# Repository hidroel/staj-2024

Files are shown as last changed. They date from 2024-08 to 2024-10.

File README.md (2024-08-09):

# Proje Başlığı: Damlama Sulama Sistemi Ek Modülü

## 1. Giriş
### 1.1 Proje Tanımı
Müşterimiz, tarım sulama sisteminde kullandığı damlama sulama sistemi ile ilgili bir sorun yaşamaktadır. Bu proje, bu sorunu tespit etmek ve çözmek amacıyla yürütülecektir.

### 1.2 Amaç ve Hedefler
Projenin amacı, damlama sulama sisteminin çalışmasında aksamaya neden olan problemleri belirlemek ve bu problemleri çözmektir. Hedefler:
- Problemin nedenlerini belirlemek
- Çözüm önerileri sunmak
- Çözümün uygulanabilirliğini test etmek
- Nihai çözümü uygulamak

## 2. Mevcut Durum Analizi
### 2.1 Problemin Tanımı
Müşterimiz, dizel su pompası çalışmakta iken su çekilen kanalda suyun kesilmesi sonucunda santifüj'ün susuz kalarak boşta çalıştığını ve yaklaşık 30 saniye sonra yanarak kullanılamaz hale geldiğini belirtmiştir. Su pompasında barometre olmasına rağmen sistemin otomatik olarak durmasını sağlayan bir araç bulunmamaktadır. Başlatma ve durdurma işlemleri tamamen manuel olarak yapılmaktadır. Müşterimiz su kesintisi durumunda sistemin durmasını ve kendisine SMS bilgilendirmesi gelmesini istemektedir.

### 2.2 Önceki Çalışmalar
Konuyla ilgili daha önce herhangi bir modül tasarımı ve uygulaması yapılmamıştır. Yalnızca geçici çözüm olarak müşterimiz su pompasının başında bekleyerek basınç düştüğünde sistemi durdurmaktadır. Bu çözüm iş gücü gerektirmesi ve efektif olmamasından dolayı müşterimiz için kabul edilmemektedir.

## 3. Çözüm Önerileri
### 3.1 Olası Nedenler ve Çözümler
Sorunun nedenleri:
- Su çekilen kanalda belirsiz saatlerde su kesintileri olması.
- Santrifüj'ün boşta çalıştığında fazla sürtünme yapması ve aşırı ısınmasın.
- Su kesintilerinin önceden bildirimi yapılmayıp tamamen plansız olması.

Çözüm Önerileri:
- Su kesintisi önceden biliniyorsa bu saatler aralığında su pompasının çalıştırılmaması.
- Su basıncının entegre bir sistem ile sürekli kontrol edilerek su kesintisi veya azalması durumunda sistemin otomatik olarak kendini durdurması.

### 3.2 Çözümün Uygulanması
En verimli çözüm belirlenmiştir ve çözümün uygulama adımları aşağıdaki gibidir:
1. Su pompası üzerinde bulunan barometre tamamen analog çalıştığı için ek bir basınç sensörü eklenecektir.
2. Basınç sensörü kanaldan gelen hortum üzerinde olacak ve su boşluğu pompaya varmadan önce durumu sisteme bildirebilecektir.
3. Basınç sensöründen uyarı geldiği anda dizel motor durdurulacak ve su çekme işi son bulacaktır.
4. Dizel motorun durdurulabilmesi için yapılacak bağlantı su pompasının aç-kapa anahtarlamasına bağlanacaktır. Su pompası dijital olarak durdurabilecektir.
5. Sistemin durmasının hemen ardından müşteriye SMS iletilecektir.

## 4. Beklenen Sonuçlar ve Ölçümler
### 4.1 Beklenen Sonuçlar
Çözüm yöntemimiz uygulandığında su kesintileri hangi saat aralığında olursa olsun kesinti olduğu anda su pompası otomatik olarak duracak ve sistemin susuz kalmasından dolayı oluşan tüm problemlerden kaçınılacaktır. Ayrıca müşteriye giden SMS sayesinde müşterimiz sistemin durduğunun haberini alarak sulama programını buna göre ayarlayabilecektir.

### 4.2 Başarı Kriterleri

- Su pompasının hiçbir bileşenlerinin susuz kalma sonuçlarından olumsuz etkilenmemesi.
- Müşterinin sulama durduğuna dair bilgiyi eksiksiz ve zamanında alması.

## 5. Zaman Çizelgesi

1. Problemin Analizi: 1 hafta
2. Çözüm Önerilerinin Geliştirilmesi: 1 hafta
3. Çözümün Uygulanması: 2 hafta
4. Test ve Gözlem: 1 hafta
Toplam: 5 hafta

## 6. Kaynaklar ve Bütçe
Projede kullanılacak malzemeler, hizmet ve işçilik maliyeti gibi değişkenler listelenecek ve toplam hesap çıkartılacak.

Tahmini bütçe: HESAPLANACAK

## 7. Kullanılacak Bileşenler

- 1x ADC
- 1x Röle
- 1x MCU (STM32F103RC)
- 1x GSM Modülü (SIM800L HZ-MG2608-C1A-MK-02)
- Yakıt Kesici (UNOX 24V DC Normalde Açık Solenoid Valf)
- 1x Basınç Sensörü (DFRobot SEN0257)
- 3x LED
- 3x Buton

### MCU İçin Gerekli Pinler
- 1x I2C
- 1x SPI
- 4x UART

### Bileşenlerin Kullanım Sebepleri

Proje diyagramında görüldüğü gibi, sistemin çalışma prensibi istenmeyen durum oluştuğunda motorun durdurularak pompanın kapanmasıdır. Kullandığımız basınç sensörü 0-16 bar aralığında olup düzenli ve sık aralıklarla suyun basıncını ölçecektir. Su kesildiğinde hat içerisinde basınç düşecek ve basıncın düşmesi MCU tarafından algılanacak ve valfe bağlı röle tetiklenecektir. Rölenin tetiklenmesi sonucunda normalde açık olan özelliğe sahip valf kapanacak ve dizel motora yakıt akışı duracaktır. Bu sayede dizel motor stop ederek santifüj'ün yanmasını engelleyecektir. MCU röleyi tetiklerken aynı zamanda GSM modülüyle haberleşme sağlayarak müşterimizin telefonuna bildirim SMS'i gitmesini sağlayacaktır.

## 8. Projenin Genel Çalışma Prensibi

Projenin sözel açıklaması şu şekildedir:

MCu'yu barındıran kart ve diğer tüm ek bileşenler dizel motorun aküsünden beslenecektir. Motora ait olan kontak akü ile modüller arasında bağlantıyı sağlamaktadır. Dizel motorun yakıt tankı ile motor arasında bulunan yakıt hortumuna solenoid valf eklenecektir. Bu valf projenin maliyetini düşürmek amacıyla normalde kapalı olarak belirlenmiştir. Solenoid valfin Vin bağlantısı MCU üzerindeki rölenin NC bacağına bağlıdır. Rölenin Common bacağı ise aküden güç almaktadır. Bu sayede, ek modülün herhangi bir sebeple devre dışı kalması durumunda dahi rölede güç akışı devam edecek ve normalde kapalı özelliğe sahip olan valf açık durumda (Yakıt geçişi mümkün) olacaktır.

Projeye özel olarak tasarlanan ek modül kartı, basınç sensörü ile 0-5v protokolü kullanarak analog haberleşme yapacaktır. 2 saniyelik periyotlar ile basınç sensöründen veriler alınarak ADC ile MCU'ya iletilecektir. MCU tarafından basınç kontrol edilerek, istenilen değerin altına düşmesi durumunda röle tetiklenecek ve dizel motor stop ettirilecektir. Bununla eş zamanlı olarak UART ile GSM modülü haberleşmesi sağlanacak ve belirlenen telefon numarasına durumla ilgili SMS gönderilecektir.

Manuel olarak kontak kapatıldığı durumda aküden gelen güç kesildiği için tüm sistem devre dışı kalacaktır. Ayrıca normalde kapalı olan valf herhangi bir tetikleme almadığı için kapalı konuma geçecektir. Bu sayede dizel motor kapalı durumdayken ekstra güvenlik sağlanmış olacaktır.
## 9. Sonuç ve Öneriler
Bu projede belirtilen çözüm adımları doğru bir şekilde uygulandığında ve gerçek uygulama testi analizlerdeki gibi gittiğinde müşterinin tüm sorunu ortadan kaldırılacaktır. Bununla birlikte, sistem uzaktan başlatma ve durdurma gibi ileriye dönük gelişmelere açıktır. Tamamen manuel olarak çalışan su pompası bu entegre ile birlikte durdurma işlemi kontrol edilebilir hale gelmiştir. İleriye dönük eklemeler ve güncellemelerle sistem insan gücünü daha az harcayacak duruma getirilebilir.

Müşteriye eklenen sensörlere ve kartlara zarar vermemesi, afaki koşullarda bulundurmaması için gerekli uyarılar yapılmalıdır. Projede kullanılan akü, kablo gibi zaman içerisinde yıpranan ve ömrünü tüketen materyaller hakkında düzenli bakım yaptırması belirtilmelidir.

Bu projede 0-5v analog haberleşme protokolü ve çevre bileşenlerle seri haberleşme protokolleri uygulanmıştır. Bunlarla alakalı detaylı bilgiye ulaşmak için:

[Seri Haberleşme Dökümanı](https://github.com/hidroel/staj-2024/blob/main/documents/serial.md)
[Analog Haberleşme Dökümanı](https://github.com/hidroel/staj-2024/blob/main/documents/analog.md)

Projede kullanılacak kartın diyagrami aşağıdadır:

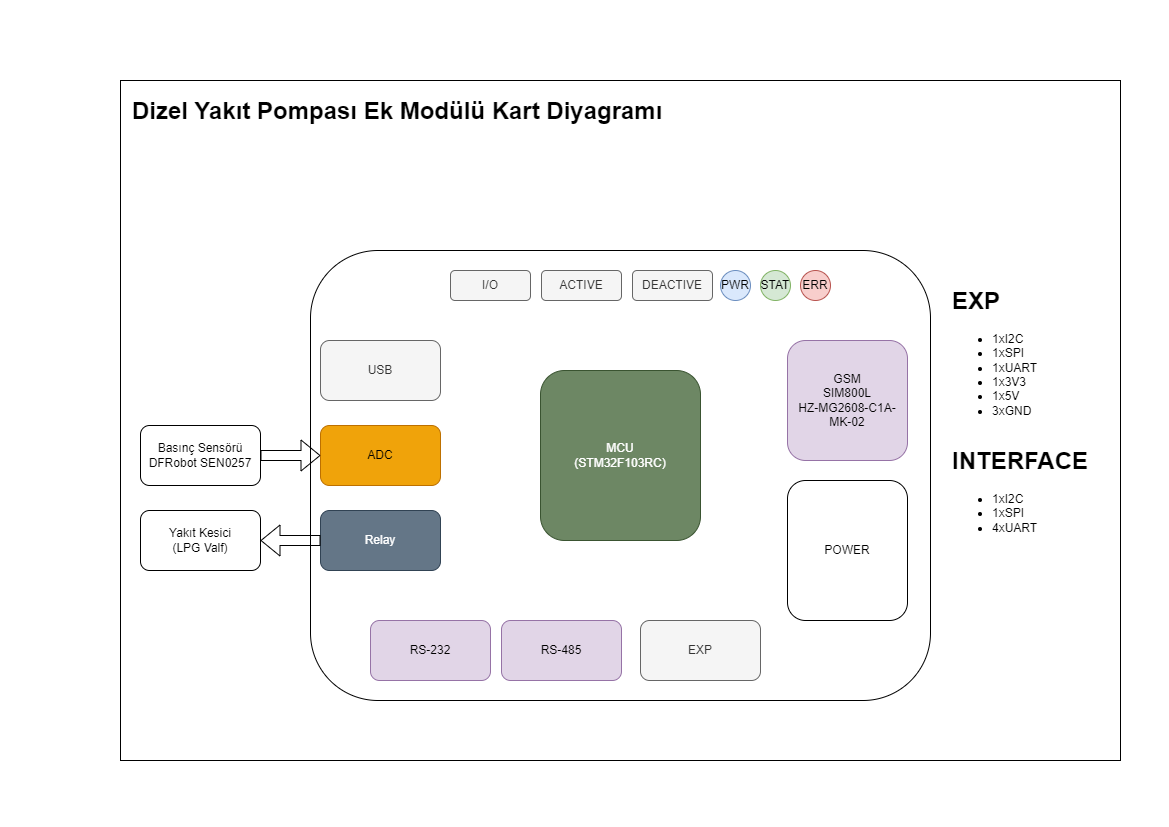
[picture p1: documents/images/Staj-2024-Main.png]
Main Diyagram


Projenin çalışma prensibini açıklayan diyagram aşağıdadır:

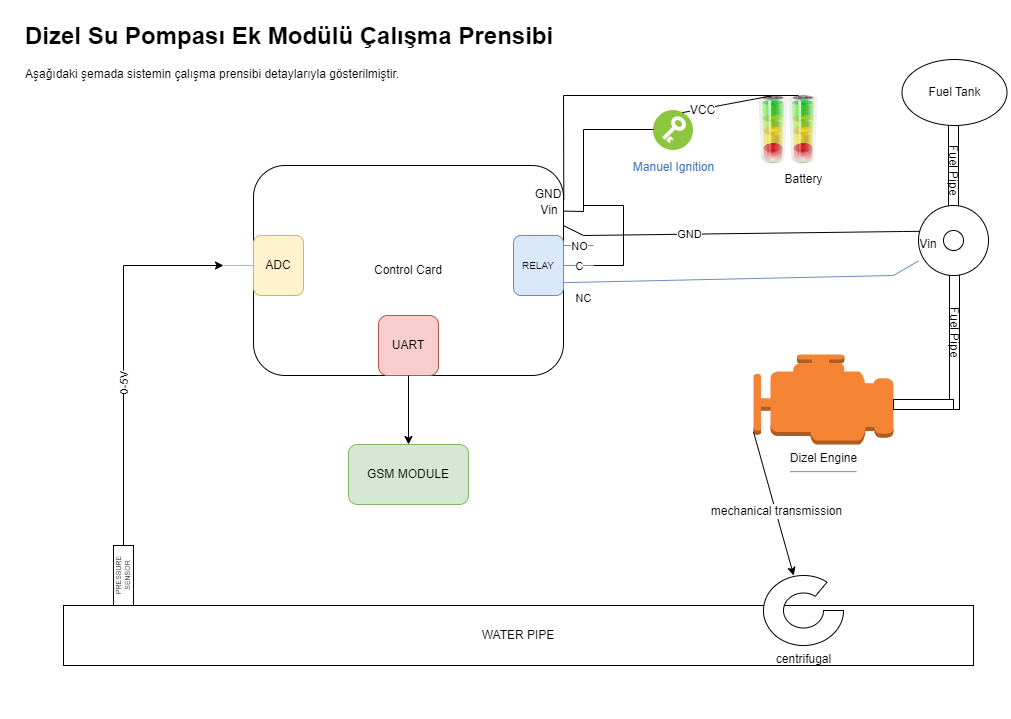
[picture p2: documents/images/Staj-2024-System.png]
System Diyagram


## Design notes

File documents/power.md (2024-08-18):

# Power Devresi Nedir?
Power devresi, bir elektronik sistemin tüm bileşenlerine gerekli enerjiyi sağlamak için tasarlanmış bir devredir. Elektronik cihazların düzgün ve güvenilir bir şekilde çalışabilmesi için doğru voltaj ve akım değerlerinin sağlanması kritik öneme sahiptir. Power devresi, bu ihtiyacı karşılamak için güç kaynaklarını düzenler, dönüştürür ve filtreler. Kart üzerindeki en önemli devredir ve sistemin işleyişi için hayati önem taşır. Power devresinde kullanılan bileşenler şunlardır:

- Güç Kaynağı: Sistemin ana gücünü aldığı ekipmandır. Adaptör, akü, pil, batarya gibi herhangi bir şey olabilir.
- Dönüştürücüler: Sistemdeki bileşenlerin ihtiyacı olan voltaj her zaman güç kaynağı ile aynı değildir. Bu nedenle voltajı istenilen seviyelere çevirmek için dönüştürücüler kullanılır. Ayrıca, AC güç kaynağı varsa DC'ye çevirir.
- Filtreler: Gürültü ve dalgalanmaları azaltarak stabil bir güç sağlar. Kapasitörler ve indüktörler ile oluşturulan filtre devreleri ile bu sağlanır.
- Koruma Devreleri: Aşırı akım çekme, yüksek voltaj, kısa devre gibi durumlarda sistemin korunabilmesi için koruma devresi oluşturulur. Sigorta gibi bileşenlerle sistemin güvenliği sağlanır.

# Filtreler
Elektronik bileşenlerin sağlıklı çalışabilmesi için parazitlerden mümkün olduğunca uzak olması gereklidir. Buna power devresi de dahildir. Güç kaynağından gelen gerilim genellikle parazitli gelmektedir. Bu da diğer bileşenlerin sağlıklı çalışmasına engel olmaktadır. Bu nedenle, power devresinde çeşitli filtreler uygulamak zorundayız.

## LC ve CL Filtreleri

LC ve CL filtreleri paraziti azaltmak ve kesintisiz bir gerilim sağlamak amacıyla kullanılır. L, indüktörü C ise kapasitörü temsil eder. LC ve CL olarak ayrılmasının sebebi ise bağlantı şekillerinin farklı olmasıdır. İhtiyaca göre LC olarak veya CL olarak kullanılırlar. 

Filtrelerde alçak geçiş filtreleri ve yüksek geçiş filtreleri olarak iki ana çeşit bulunmaktadır. Düşük geçiş filtresi, belirli bir kesim frekansının altındaki sinyalleri geçiren, kesim frekansının üstündeki sinyalleri ise bastıran bir filtre türüdür. Yüksek geçiş filtresi ise belirli bir kesim frekansının üstündeki sinyalleri geçiren, kesim frekansının altındaki sinyalleri ise bastıran bir filtre türüdür. Projemizin power devresini yaparken aküden çıkan gerilimi sabit halde alabilmek için kullanacağımız filtre alçak geçiş filtresi olacaktır. Alçak geçiş filtrelerinin çeşitlerine şematik olarak bakalım.

#### CL Tipi Filtre
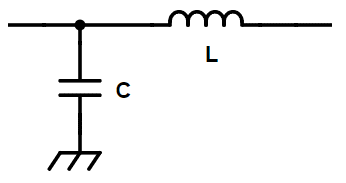
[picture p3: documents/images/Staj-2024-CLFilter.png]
CLFilter

Giriş empedansı yüksek, çıkış empedansı düşük olduğunda kullanılır.
#### LC Tipi Filtre
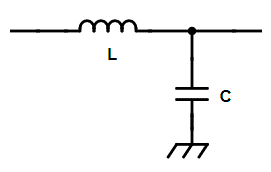
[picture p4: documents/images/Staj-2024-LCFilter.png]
LCFilter

Giriş empedansı düşük, çıkış empedansı yüksek olduğunda kullanılır.
#### Pi Tipi Filtre
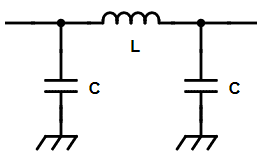
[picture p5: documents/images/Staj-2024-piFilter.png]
PiFilter

Giriş empendansı ve çıkış empadansı yüksek olduğunda kullanılır.
#### T Tipi Filtre
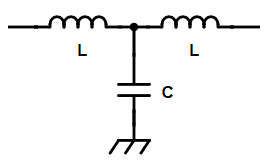
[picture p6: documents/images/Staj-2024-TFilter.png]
TFilter

Giriş empendansı ve çıkış empadansı düşük olduğunda kullanılır.

İhtiyaca göre bu filtrelerden herhangi birisi kullanılabilir. Bu projenin power devresinde 12v çıkışı için pi tipi ve LC tipi filtre kullanabilirdik. Biz pi tipi filtre kullanmayı seçtik. Bunun sebepleri:

- Pi tipi filtreler daha geniş bir frekans aralığında filtreleme yapabildiği için daha net bir parazit temizliği yaparlar.
- Power'dan sonraki ilk filtre olarak kullanacağımızdan dolayı maksimum netlikte güç almamız gerekiyor.
- LC filtre ile arasında yalnızca bir kapasitörlük maliyet farkı bulunuyor. Bu düşük maliyet farkı proje bütçesini etkilemiyor.

# Voltajı Regüle Etmek
Projemizde 12v bir akü tarafından güç alıyoruz ancak 5v ve 3.3v ile çalışan bileşenler mevcut. Bundan dolayı 12 voltu hem 3.3v hem de 5v olarak düşürmemiz gerekiyor. Bu işleme "regüle" adı veriliyor. Voltaj regülesini yapmanın birden fazla yolu var. Şimdi bunlara kısaca değinelim ve projede hangi yöntemi kullanacağımızı açıklayalım.

### Anahtarlamalı Regülatörler
Anahtarlamalı regülatörler, voltajı düşürmek için bir anahtarlama elemanı (genellikle MOSFET) kullanır. Giriş voltajı hızlı bir şekilde açılıp kapanarak enerji düzenlenir ve endüktörler ile kapasitörler kullanılarak çıkış voltajı istenilen seviyede tutulur. Bu yöntem yüksek verimlilik ve geniş giriş voltajı aralığı sağlar.

### Doğrusal Regülatörler
Doğrusal regülatörler, voltajı düşürmek için bir direnç kullanarak giriş voltajı ile çıkış voltajı arasındaki farkı kaybederler. Bu yöntem, çıkış voltajını oldukça stabil tutar, ancak verimliliği genellikle düşük olur çünkü fazla enerji ısı olarak yayılır.

### Zener Diyot Regülatörleri
Zener diyot regülatörleri, bir zener diyotu kullanarak voltajı sabitler. Giriş voltajı, zener diyotun ters yönde çalışmasını sağlayacak şekilde seçilir ve bu diyot, belirli bir voltajda sabitler. Bu yöntem genellikle düşük akım uygulamaları için uygundur.

Voltajı düşürmek veya yükseltmek için bunların haricinde de yöntemler bulunuyor ancak yaygın kullanılan ve bu projede kullanılması potansiyel olan seçenekler bunlar. Her birinin kendine göre kullanım alanları mevcut.

Projemizde anahtarlamalı regülatörler kullanacağız. Bunun birden fazla sebebi var:

- Akünün giriş voltajı sabit olarak 12v olmayacak. Akü tam şarjda iken 13 voltlara kadar çıkabilirken, akü deşarj olurken 9 voltlara kadar düşecektir. Bu nedenle bize geniş giriş aralığına sahip bir regülatör gerekiyor.
- Doğrusal regülatörler ve zener diyotlar sistemin verimliliğini oldukça düşürmektedir. Boşa giden güç ısıya dönüşerek aynı zamanda sistemin ısınmasını sağlamaktadır. Eğer küçük miktarlarda düşüş yapacak olsaydık tercih edilebilirdi ancak 5v ve 3.3v'a regüle etmek için projemize uygun değiller.
- Anahtarlamalı regülatörler güç kaybını minimuma indirerek akımın korunmasını sağlarlar. Bu sayede oldukça az ısınma yaparlar.

### Anahtarlı Regülatör Kullanımı
Anahtarlı regülatörler bir entegreden ve yan bileşenlerden oluşur. Entegre hazır olarak alınır, sonrasında ise çevre bileşenlerin devreleri çizilerek çalışır hale getirilirler. Kullanılacak entegrenin datasheet'inde yer alan çevre bileşenlere göre bir devre çizimi yapılabilir. Çevre bileşenlerde genellikle endüktör, kapasitör, diyot kullanılır. 

**Önemli Not:**Kullanılan diyotun sebep olduğu voltaj kaybını hesap ederek sistemi oluşturmak oldukça önemlidir. Diyot üzerinden yük geçişi olduğunda bir miktar voltaj kaybına sebep olur.

# Güvenlik Sistemleri

## Aşırı Gerilim Koruma Devresi

Aşırı gerilim koruma devresi oluşturmak ve kullanmak için öncelikle gerekli bileşenleri seçmeliyiz. Genellikle, bir voltaj referansı olarak Zener diyot veya voltaj referansı, bir komparatör ve bir anahtar elemanı (MOSFET veya röle) kullanıyoruz. Komparatörün pozitif girişine Zener diyotun katodunu bağlayıp, anotunu giriş voltajına bağlıyoruz. Komparatörün negatif girişine ise giriş voltajını bağlıyoruz. Komparatörün çıkışını anahtar elemanına bağlayarak, aşırı voltaj algılandığında devreyi açacak şekilde düzenliyoruz. Eğer MOSFET kullanıyorsak, gate pinini komparatör çıkışına, source pinini toprağa ve drain pinini yükünüzün toprak hattına bağlıyoruz. Röle kullanıyorsak, rölenin bobinini komparatör çıkışına bağlıyoruz. Devreyi test ederken, giriş voltajını yavaşça artırarak Zener diyot üzerindeki voltajı izliyoruz ve voltaj eşiğine ulaşıldığında komparatör çıkışının değişip değişmediğini, MOSFET'in açılıp açılmadığını veya rölenin çekilip çekilmediğini kontrol ediyoruz. Bu adımları izleyerek, aşırı gerilim durumlarında sisteminizi otomatik olarak koruyabiliyoruz.
## Aşırı Akım Koruma Devresi 

Aşırı akım koruma devresi oluşturmak ve kullanmak için öncelikle uygun bileşenleri seçmeliyiz. Genellikle, bir akım sensörü veya şönt direnç, bir komparatör ve bir anahtar elemanı (MOSFET veya röle) kullanıyoruz. Akım sensörü veya şönt direnci, akımı ölçmek için kullanılır ve bu ölçüm, komparatörün bir girişine bağlanır. Komparatörün diğer girişine, belirlenen akım eşiğini temsil eden bir referans voltajı bağlarız. Komparatörün çıkışını anahtar elemanına bağlayarak, aşırı akım algılandığında devreyi açacak şekilde düzenleriz. Eğer MOSFET kullanıyorsak, gate pinini komparatör çıkışına, source pinini toprağa ve drain pinini yükünüzün toprak hattına bağlıyoruz. Röle kullanıyorsak, rölenin bobinini komparatör çıkışına bağlıyoruz. Devreyi test ederken, akım seviyesini yavaşça artırarak şönt direncin üzerindeki voltajı izleriz ve akım eşiğine ulaşıldığında komparatör çıkışının değişip değişmediğini, MOSFET'in açılıp açılmadığını veya rölenin çekilip çekilmediğini kontrol ederiz. Bu adımları takip ederek, aşırı akım durumlarında sisteminizi otomatik olarak koruyabiliriz.

## Kısa Devre Koruması
Kısa devre durumunda sistem çok yüksek akım çekeceği için aşırı akım koruma devresi bağlantıyı kesecek ve sistemi koruyacaktır. Tepki süresi boyunca geçen sürede bazı ekipmanlar zarar görebilir. Zararı minimuma indirmek için aşırı akım koruma devresinde tepki süresini minimize edecek bileşenler kullanmalıyız.

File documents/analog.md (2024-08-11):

# ADC Nedir?

ADC'ler analog olan sinyali dijitale dönüştüren araçlardır. Gelen sinyalin voltaj değerine göre dijital bir çıktı verir. ADC'lerin hemen hemen hepsi 0-5v aralığında çalışır. Bundan dolayı analog sensörler genelde 0 - 5v aralığındadır. MCU gelen veriyi dijital olarak okuyabildiği için herhangi bir sensörden veri okurken ADC kullanılarak analog olan veri dijitale çevirilerek MCU'ya aktarılır. Basit bir deyişle MCU'nun anlayacağı dilde aktarılır.

# ADC Türleri

- **Çift Eğimli** - Ucuz ve çok yavaş
- **Flaş** - Çok hızlı ama bit çözünürlüğü düşük
- **Boru hattı** - Çok hızlı ama bit çözünürlüğü düşük
- **SAR** - Hızı ve çözünürlüğü iyi (Çok tercih edilen)
- **Delta Sigma** - Hızı ve çözünürlüğü iyi

# Bit Çözünürlüğü

Yüksek bit çözünürlüğünde adım aralıkları daha kısadır. Yani daha hassas ölçümler yapılabilir. Bit çözünürlüğü düştükçe adımların aralığı artacağından gelen verinin hassasiyeti azalır.

# 4-20 mA Protokolü

4-20 mA bir dijital iletişim protokolüdür. Adından da anlaşıldığı gibi 4 ile 20 mA arasında akım değerleriyle haberleşme sağlar. Toplam 16 mA'lık bir aralığı bulunur. 0-5v, 0-10v gibi diğer analog ölçüm çeşitlerine göre avantajları ve dezavantajları vardır. 4 mA en alt seviyeyi, 20 mA ise en üst seviyeyi temsil eder. Sensörden gelen veri tipine bağlı olarak uygun aralıklama yapılır.

4-20 mA akım kaynaklı bir haberleşme çeşidi olduğu için güç kaynağından kesintisiz ve sabit akım alması gereklidir. Bu sağlandığında taktirde veri bozulmadan ve gürültü olmadan uzun mesafelerde yol kat edebilir. Voltaj kaynaklı haberleşmelerde mesafe uzadıkça gürültü artacaktır ve verinin doğruluğu kaybolacaktır.

4-20 mA'da 4 mA altına inme veya 20 mA üstüne çıkma durumu olursa sistemde bir hata olduğuna işaret eder. Gelen veri doğru kabul edilmez.

# 4-20 mA ADC İle Okuma

ADC'lerin büyük bölümü voltaj ile okuma yaparlar. 4-20 mA ise akım ile veri aktarımı sağlar. Bundan dolayı ADC ile bu verinin okunabilmesi için voltaj aralıklarına dönüştürülmesi gereklidir. Veri iletim hattı 4-20 mA protokolü ile ADC'ye kadar gelir. ADC'ye aktarılmadan önce bir direnç devresi kurularak akıma bağlı voltaj değişikliği sağlanır. Bu aşamada genellikle 250 ohm direnç kullanılmaktadır. Bu voltajı ADC okur ve dijitale çevirerek MCU'ya iletir.

4-20ma Görseli

# 0-5v Protokolü
0-5v protokolü, gerilim ile veri iletimi sağlayan bir protokoldür. Sensörden çıkan gerilim 0 ile 5v arasında olmak zorundadır. Sensörün ölçüm aralığına göre 0-5v arasında bir gerilim çıkışı yapar ve bu ADC tarafından okunur. Örneğin 0-100 derece arasında sıcaklık ölçen bir sıcaklık sensörü 0-5v protokolü kullanıyorsa 0 derece 0 volta, 50 derece 2,5 volta, 100 derece ise 5 volta karşılık gelecektir. ADC'ler gerilim kaynaklı okuma yaptığı için ekstra herhangi bir dönüşüm yapmaya gerek kalmamaktadır.

# 0-10v Protokolü
0-10v protokolü 0-5v ile aslında birebir aynıdır. Çalışma prensibinde hiçbir farklılık yoktur. Aradaki tek fark aralığın daha geniş olması yani 0-10v arasında olmasıdır. Bu sayede daha fazla parçalama yapılabilir ve ölçüm hassasiyeti artırılabilir. Tabii bu hassasiyet için ADC'nin çözünürlüğünün de buna uygun olması gereklidir.

0-5v Görseli

0-5v 0-10v Farkı

# Diferansiyel ve Tek Uçlu Bağlantılar
Tek Uçlu (Single-Ended) Bağlantı: Bu bağlantı türü, bir analog sinyalin referans olarak ortak bir toprak hattına (GND) karşı ölçüldüğü bir yöntemdir. Tek bir giriş hattı ve bir toprak hattı kullanılır. Bu, basit ve yaygın olarak kullanılan bir yöntemdir, ancak gürültüye karşı hassas olabilir.

Diferansiyel Bağlantı: Diferansiyel bağlantıda, iki giriş hattı (pozitif ve negatif) kullanılır ve sinyal bu iki hat arasındaki fark olarak ölçülür. Bu yöntem, ortak mod gürültüsünü (örneğin elektromanyetik girişim) ortadan kaldırarak daha güvenilir ve doğru ölçümler sağlar. Özellikle uzun mesafelerde veya gürültülü ortamlarda tercih edilir.

# Çoklama
Analog Multiplexer (Çoklayıcı): Çoklayıcılar, tek bir ADC (Analog to Digital Converter) kullanarak birden fazla analog sinyali okumanın bir yolunu sunar. Çoklayıcı, giriş sinyalleri arasında hızla geçiş yaparak birden fazla kaynaktan gelen verileri tek bir ADC üzerinden işler. Bu, çok kanallı sistemlerde maliyetleri düşürmek için kullanılır.
# Paralel Bağlantılar

Paralel bağlantı, aynı anda birden fazla sinyalin iletilmesi için kullanılır. Bu yöntemde, her bir sinyalin kendi hattı vardır, bu da daha hızlı veri iletimine olanak tanır, ancak daha fazla kablo gerektirir.

# Aktif Pasif Filtreleme
Aktif Filtreleme: Bu yöntemde, sinyal işlemeyi geliştirmek için aktif bileşenler (örneğin, op-amp'ler) kullanılır. Aktif filtreler, belirli frekanslardaki gürültüyü azaltarak sinyal kalitesini artırabilir ve sinyalin daha hassas bir şekilde işlenmesini sağlar.

Pasif Filtreleme: Pasif bileşenler (dirençler, kapasitörler, indüktörler) kullanılarak yapılan filtreleme, genellikle daha basittir ve güç gerektirmez. Pasif filtreler, istenmeyen frekansları ve gürültüyü bastırmak için kullanılır, ancak aktif filtreler kadar esnek değildirler.

# Analog Demodülasyon
Analog sinyallerin farklı taşıyıcı frekanslar üzerine bindirilip, daha sonra demodüle edilerek asıl bilgiye erişildiği bir yöntemdir. Bu, özellikle radyo frekansı iletişimlerinde kullanılır.

# Zaman Bölmeli Çoklama
Birden fazla analog sinyalin, belirli zaman dilimlerinde sırayla tek bir hat üzerinden iletilmesi yöntemidir. Her sinyal belirli bir zaman aralığında gönderilir ve bu zaman dilimleri arasında geçiş yaparak birden fazla sinyalin tek bir hat üzerinden iletilmesi sağlanır.

# ADC Bit Çözünürlüğü Önemi

ADC'ler 8 bit, 10 bit, 16 bit gibi birçok farklı bit çözünürlüğüne sahiptir. Bit çözünürlüğü kullanım alanına göre oldukça önemlidir. Bit çözünürlüğü ADC'nin dijital adım sayısının belirtir. 2 üzeri bit sayısı şeklinde adım sayısı bulunur. Örneğin 8 bitlik bir ADC 256 adım aralığına sahiptir. 16 bitlik bir ADC 65536 adım sayısına sahiptir. Adım sayısı sensörlerden okunan verinin hassasiyetini belirler. Örneğin 0-256 PSI aralığında basınç ölçen bir sensördeki veri 8 bitlik bir ADC ile okunursa basınç değişimleri 1 PSI olarak değişir, ara değerler ölçülemez. Bu sensördeki veri 16 bitlik bir ADC ile okunursa 0,01 PSI gibi küçük değerlerin değişimi bile dijital olarak okunabilir.

Bir sensörden veri okunduğunda ADC bunu dijital bir sayısal değere çevirerek MCU'ya aktarır. Bu sayede MCU tarafından sensörden gelen veri doğru bir şekilde yorumlanabilir.

# STM32 İle ADC Kullanımı

ADC, STM32 ile denetleyicilerin üzerinde dahili olarak bulunmaktadır. Seçilen MCU modeline göre ADC'nin kaç bit çözünürlüğe sahip olduğu öğrenilmelidir.

Kullanılan MCU'nun datasheet'inde hangi pinlerin ADC olarak kullanılabileceği belirtilmiştir. Öncelikle buradan pin seçimi yapılmalıdır. Ardından bu pin STM32Cube ile ADC olarak yapılandırılmalıdır. Sonrasında ADC'nin çözünürlüğü (bit) yapılandırılmalıdır. Daha sonra Hz cinsinden örnekleme hızı yapılandırılmalıdır. Bu örnekleme hızı ADC'nin saniyede kaç kere analog veriyi dijitale çevireceğini belirler. Projenin ihtiyacına göre burada frekans ayarlaması yapılır.

İlgili sensörün standart VCC GND bağlantıları yapıldıktan sonra analog çıkışı STM32'nin ADC olarak belirlenen pinine bağlanır. Gerekli diğer ayarlar da yapıldığı için bu aşamadan sonra ADC belirtilen sürelerde sensörden gelen analog veriyi dijitale yani sayısal bir biçime çevirerek MCU'ya aktarır. Sensörün ölçüm aralığına göre dijital aralıkların karşılığı hesaplanır ve istediğimiz birimde ölçüm sonucunu alabiliriz. Bu aşamadan sonra MCU'nun sensörden gelen veriye göre ne yapacağı projeye göre belirlenebilir.

Eğer projede birden fazla analog veri toplanacaksa MCU'nun diğer GPIO pinleri de ADC olarak tanımlanıp her birinden farklı kanallar üzerinde veri toplanabilir. Bu sayede tek bir MCU ile birden fazla sensörden veri alınarak yorumlanabilir.

> Not: STM işlemciler genellikle SAR tipi ADC kullanmaktadır.

# ADC'yi Verimli Kullanmak İçin Yapılabilecekler

- ADC pinlerinin girişinde çok küçük (0,1 uF) kapasitörler koyularak gürültü azaltılır.
- Analog veri hattı mümkün olduğunca kısa tutularak gürültü azaltılır.
- Analog veri hattı manyetik alan üreten bileşenlerden uzak tutularak manyetik gürültüden korunur.
- Analog sinyal yolları dijital sinyal yollarıyla çok yakın olmamalıdır.

# Tarım Sulama Sistemi Ek Modülü ADC Kullanımı
Projemizde kullandığımız basınç sensörünün analog çıkış gerilimi 0.5v ile 4.5v arasındadır. ADC olarak MCU üzerindeki dahili ADC'yi kullanacağımız için bu aralık ihtiyacımızı karşılamamakta. MCU üzerindeki dahili ADC maksimum 3.3v gerilime kadar desteklediği için sensörün kendi aralığını kullanamıyoruz. Bundan dolayı, bu gerilim aralığını 0 - 3.3v aralığına düşürmemiz gerekiyor. Gerilimi istediğimiz aralığa düşürmek için iki adet yöntem bulunuyor.

## Gerilim Bölücü Kullanımı

Gerilim bölücü basit bir devre ile sağlanmaktadır. Bu devre en temel ohm yasasına göre, gerilimin dirençle orantılı geçeceğine dayanarak kurulur. Bu sayede gerilim oransal olarak azaltılabilir. Aşağıda gerilim bölücü devresinin şemasını görebilirsiniz.

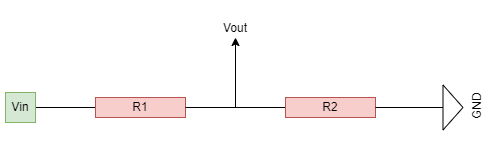
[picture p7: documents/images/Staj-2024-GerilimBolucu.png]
GerilimBolucuDiyagram


Şekilde ifade edilen R1 ve R2 dirençleri ihtiyaca uygun şekilde belirlenmelidir. Bunu hesaplamak için genel bir formül bulunmaktadır.

Bu formüller esasında V = I * R formülünden türetilmektedir. Şimdi gerilim bölücünün genel formülüne bakalım.

Vout = Vin * (R2/R2+R1)

Bu formülde gerekli yerleştirmeler yapılarak giriş voltajı istenilen çıkış voltajına getirilebilir. Ancak projemizde sabit bir gerilim değil, değişken bir gerilim var. Çünkü sensörden analog veri okuması yapacağız. Bu durumda belli bir aralığa düşürecek şekilde bir çözüm uygulamamız gerek. Bunu da şu şekilde yapabiliriz:

Vin aralığı: 0.5v - 4.5v
Vout aralığı: 0v - 3.3v 

Voutmax / Vinmax hesaplamasını yaptığımız 0.733 oranına ulaşıyoruz. Bu, gelen her değeri 0.733 ile çarparak düşürmemiz anlamına geliyor. Gerilim düşürmesini ise gerilim bölücü devresi ile sağlayacaktık. Yani, Vin değerini çarpmamız gereken sayıyı bulmuş olduk. Ana formüle baktığımızda Vin'in R2/R2+R1 ile çarpıldığını görüyoruz. Öyleyse;

R2/R2+R1 = 0.733
Gerekli matematiksel işlemler yapıldığında R2/R1 oranı yaklaşık olarak 2.74 yapmaktadır. Bu oranı sağlayacak 2 adet direnç değeri belirleyerek gerilim bölücü devresini tamamlayabiliriz. Örneğin;

R1 = 1k Ohm
R2 = 2,74k Ohm 

Özetle, projemiz için gerilim bölücü devresi kullandığımızda R1 direnci 1k Ohm, R2 direnci 2,74k Ohm kullanılarak 0.5v - 4.5v aralığı 0 - 3.3v aralığına uygun hale gelecektir. Örneğin 4.5v olan maksimum sensör verisi, ADC'ye girerken 3,2985 yani 3.3v gibi bir değerle girecektir. 

**Not:** Kullanılacak direnç değeri tam olarak bulunmaz ise seri bağlantı yapılarak birden fazla dirençle tek bir R1 direnci veya R2 direnci üretilebilir. Ancak dirençlerin sapma aralıklarının iyi ölçülmesi gereklidir.

Gerilim bölücülerin en büyük dezavantajı analog verideki hassasiyetin azalmasıdır. Geniş aralıkta olan veriyi dirençler kullanarak dar aralığa düşürdüğümüz için aralıklar azalacak yani hassasiyet azalacaktır. Büyük hassasiyet gerektiren projeler için gerilim bölücü devresi kullanmak uygun bir yöntem değildir. Bu projede bu kadar ciddi hassasiyete ihtiyaç duymadığımız için gerilim bölücü devresini rahatlıkla kullanabiliriz.

## Op-Amp Kullanımı

Gerilimi istediğimiz aralığa düşürmenin bir diğer yolu da Op-Amp kullanmaktır. Op-Amp gerilim bölücüye kıyasla daha maliyetli ancak daha hassas sonuçlar veren bir çözümdür. Gerilim bölücünün yaptığı işin aynısını başka methodlar ile yapmaktadır. Op-Amp görseli aşağıdadır: 

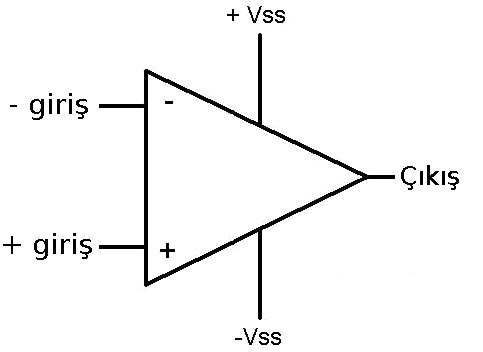
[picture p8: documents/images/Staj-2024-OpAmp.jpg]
OpAmpDiyagram


Op-Amp'ın kullanımına gelecek olursak;

 +Giriş (Non-Inverting Input):

Op-amp'in bu pinine uygulanan voltaj, çıkış voltajını belirleyen ana sinyaldir. Bu pin, sinyalin doğrudan amplifiye edildiği giriştir. Eğer op-amp'in çıkış voltajını belirlemek için sinyali bu pin aracılığıyla verirsen, op-amp bu voltajı amplifiye eder ve çıkışta uygun gerilimi sağlar.
-Giriş (Inverting Input):

Bu pin, op-amp'in giriş voltajlarının ters yönlü etkisini ifade eder. Non-inverting pin ile bu pin arasındaki fark, op-amp'in çıkışını belirler. Eğer bu pinin voltajı artırılırsa, çıkış voltajı azalır ve tam tersi.Eğer Op-amp'in çıkış voltajını bu pin ile geri besleyerek, sinyali ters yönde kontrol edebilir veya belirli bir kazanç ayarı yapabiliriz.

+Vss (Pozitif Besleme Voltajı):

Op-amp'in çalışması için gerekli pozitif besleme voltajını sağlar. Op-amp'in çalışma aralığını belirler ve çıkış voltajının üst sınırını belirler. Op-amp'in doğru şekilde çalışabilmesi için yeterli pozitif besleme voltajı sağlamalıyız.

-Vss (Negatif Besleme Voltajı):

Op-amp'in çalışması için gerekli negatif besleme voltajını sağlar. Çıkış voltajının alt sınırını belirler. Negatif besleme voltajı, op-amp'in sinyalleri doğru şekilde işleyebilmesi için gereklidir. 

Çıkış (Output):
Op-amp'in işlem sonucunda elde ettiği amplifiye edilmiş voltajı bu pin üzerinden dışarıya verir. Bu pin, diğer devre elemanları ile bağlantı kurarak, işlem sonucunu sağlar. Çıkış voltajı, op-amp'in amplifiye ettiği sinyal olup, bu voltajı ADC'ye bağlayabiliriz.

Op-Amp kullanımında gain yani kazanç hesaplaması yapılarak yükseltme ve düşürme uygulanabilir. Op-Amp genellikle yükseltme işlemlerde daha sık tercih edilir ancak düşürme için de kullanılabilmektedir. Kazanç aslında pozitif bir terimdir ancak kazancı 1'den küçük bir değer olarak belirlediğimizde düşürme işlemi için Op-Amp kullanabiliriz.

**Not:** Inverting Amplifier voltaj yükseltme anlamına gelmektedir.
**Not:** Non-Inverting Amplifier voltaj düşürme anlamına gelmektedir.

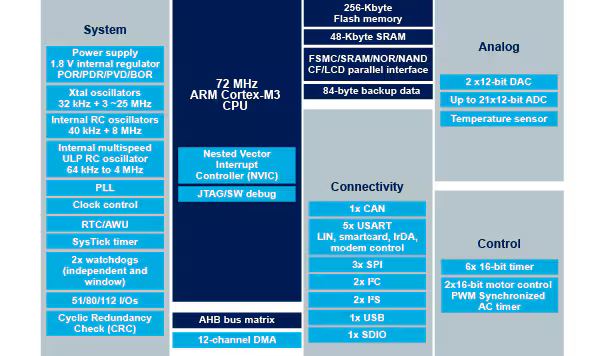
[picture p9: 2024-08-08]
hardware/docs/circuit-diagram.png

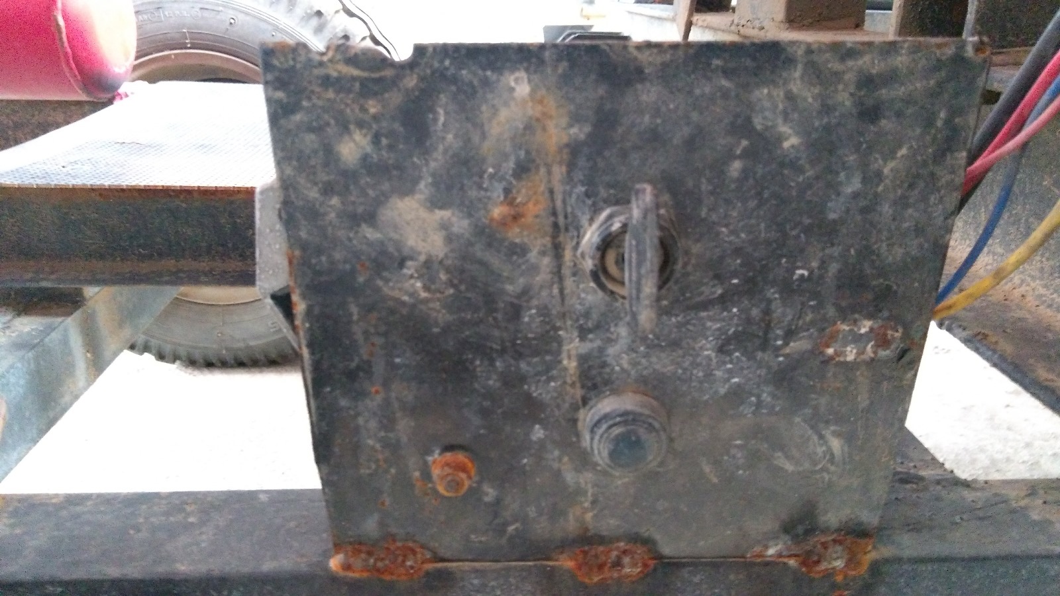
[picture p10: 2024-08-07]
documents/images/gercekfoto4.jpg

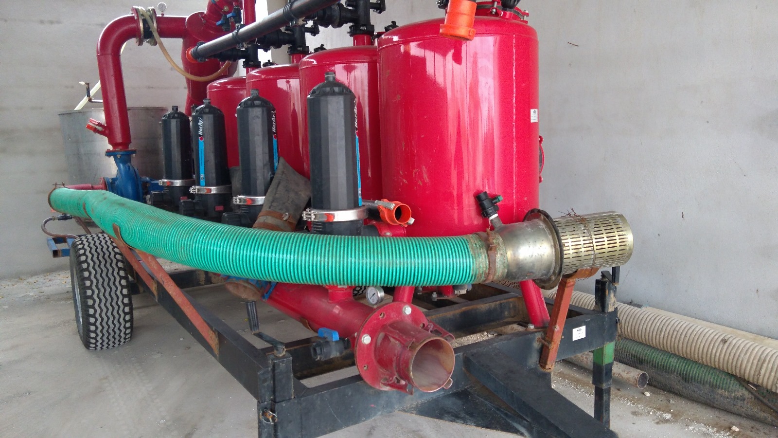
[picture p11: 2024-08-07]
documents/images/gercekfoto3.jpg

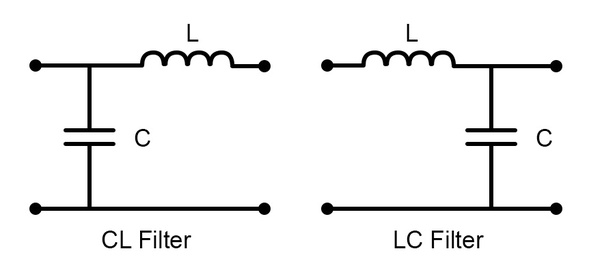
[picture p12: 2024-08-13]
documents/images/Staj-2024-Filters.jpeg

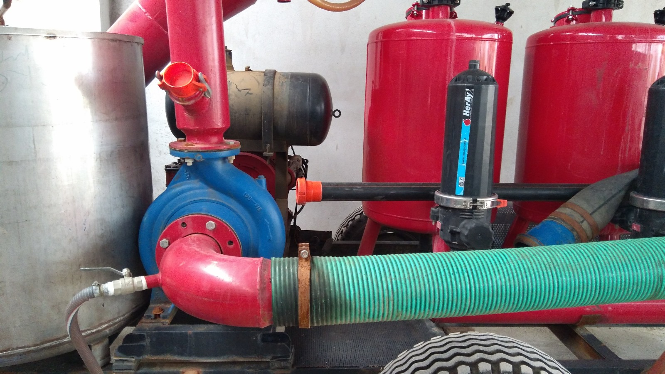
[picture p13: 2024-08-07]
documents/images/gercekfoto2.jpg

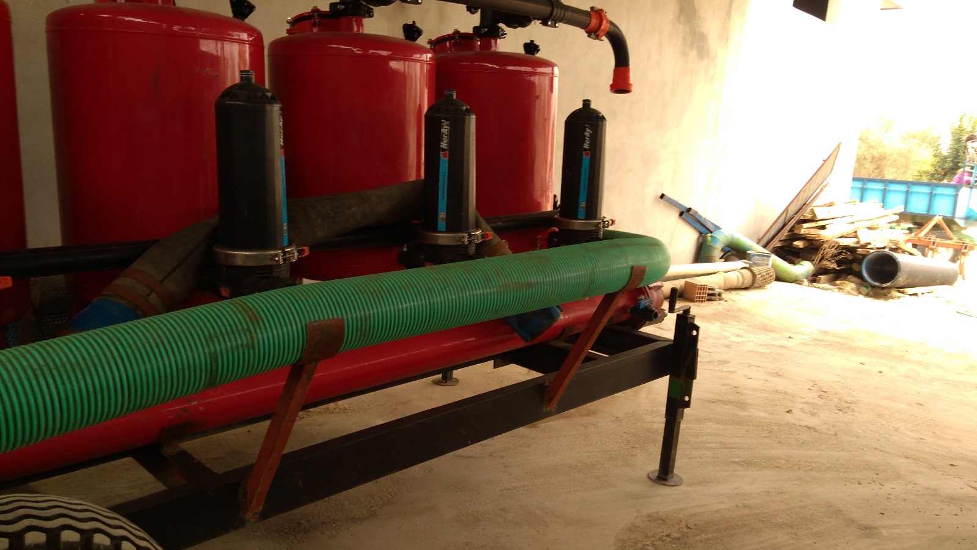
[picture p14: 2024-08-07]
documents/images/gercekfoto1.jpg

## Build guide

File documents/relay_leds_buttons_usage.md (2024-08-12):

# Röle Nedir?
Röle, yüksek akım ve gerilime sahip hatları düşük akımla anahtarlamamızı sağlayan bir devre elemanıdır. İçerisinde bulunan bobin yardımıyla bu anahtarlama işlemi gerçekleşir.

Rölenin NO (Normally Open), NC (Normally Close) ve C (Common) bacakları bulunur. Ayrıca bobini tetikleyebilmek amacıyla bobin bacakları bulunur.
Rölenin NO bacağı, bobine herhangi bir sinyal verilmediğinde açık olan bacaktır. NC bacağı ise, bobine sinyal verilmediğinde kapalı olan bacaktır. Common bacağı ise çıkış yüküne bağlanması gereken ortak bacaktır. Aşağıda rölenin şemasına yer verilmiştir:

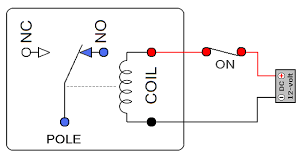
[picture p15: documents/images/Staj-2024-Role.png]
RoleDiyagram


Kontrol edeceğimiz bileşeni Common ucuna bağlamalıyız. Ardından bu bileşenin sürekli güç alıp almama durumuna göre NO veya NC bacaklarını belirleyip güç kaynağını bu bacaklardan birine bağlamalıyız. Bobin bağlantılarını ise MCU ile denetleyeceğiz.

## MCU İle Röle Bobini Kullanımı
MCU'nun dijital out pini doğrudan bobine bağlanamaz, bu oldukça riskli ve hatalı bir işlemdir. Olası riskler:

-Röle bobininde tersine voltaj dalgalanmaları olabilir ve bu MCU'ya çarparak bozulmasına sebep olur.
-Bobin MCU'nun kaldırabileceğinden daha fazla akım çekebilir ve MCU'yu yakabilir.

Her iki durum da oldukça yaşanması muhtemel durumlardır. Bu sebeple röleyi MCU ile doğrudan kontrol etmeyiz. Öncelikle bir röle sürücü devresi oluştururuz. Bu devre içerisinde transistörler ve diyotlar içerir. Transistör sayesinde yüksek akım çekilme ihtimalini ortadan kaldırırız. Diyot ise tek yönlü geçişe izin verdiği için tersine olan tüm dalgalanmaları emecek ve MCU'yu koruyacaktır.

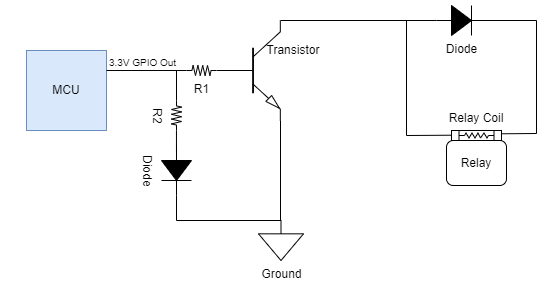
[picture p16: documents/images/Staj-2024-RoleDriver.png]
RoleDriverDiyagram


Yukarıdaki gibi bir sürücü devresi oluşturulduğu zaman MCU ile güvenli bir şekilde röle kontrolü yapılabilir.

**Not:** Kullanılacak diyot ve dirençler MCU'ya göre ve projenin diğer bileşenlerine göre değişkenlik gösterir. 

# MCU ile LED Kontrolü

LED'ler 5v, 3.3v gibi değerlerle çalışabilirler, çektikleri akım ise fazla yüksek değildir. Ancak buna rağmen doğrudan MCU ile LED sürmeye çalışmak sağlıklı bir yöntem değildir. Bu yüzden LED kontrollerinde de doğrudan MCU'ya bağlamak yerine bir sürücü devresi oluşturarak bağlantı sağlarız. Bu sürücü devresi röle kadar karmaşık değildir, bir mosfet kullanarak bu işlem sağlanabilir. Aşağıda LED sürmek için ideal bir devre şemasına yer verilmiştir.

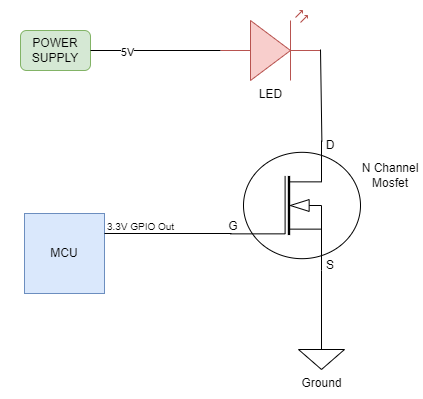
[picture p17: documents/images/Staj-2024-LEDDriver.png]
LEDDriverDiyagram


Buradaki amaç, LED'in MCU'dan değil güç kaynağından beslenmesidir. MCU yalnızca aradaki anahtarlamayı sağlayan çok düşük akımlı sinyali mosfete göndermektedir.

# MCU ile Buton Okuma
MCU'ya fiziki olarak müdahale edeceğimiz durumlar varsa butonlara ihtiyacımız var demektir. Butonlar, aslında mekanik anahtarlardır. Aktif duruma getirildiğinde anahtar kapanarak üzerinden yük geçişine izin verir. Yükteki değişimi kontrol ederek buton yardımıyla MCU'ya talimatlar verebiliriz.

Butonları devreye bağlama şeklimize göre veya butonun çeşidine göre pull up veya pull down olarak yönetebiliriz. Detaylara bakacak olursak;

## Pull Up Buton
Pull up buton, butona basılı değilken MCU'ya sürekli 1 sinyalini gönderen butondur. Dijital olarak aktif 1 gönderir. Butona basıldığı taktirde sinyal kesilir.
## Pull Down Buton
Pull down buton, pull up butonun tam tersi mantık ile çalışır. Butona basılı değilken MCU'ya herhangi bir şey göndermez. Başka bir değişle 0 olarak okuyabiliriz. Butona basıldığı anda sinyal gönderir.

Projenin kullanım alannıa göre butonlar pull up veya pull down olarak kullanılabilir. Butondan gelen hat, MCU'nun herhangi bir GPIO pinine bağlanarak dijital okuma sağlanabilir.

Bu projede pull down buton kullanmak ihtiyacımızı karşılayacaktır. Pull down butonun şeması aşağıdadır:

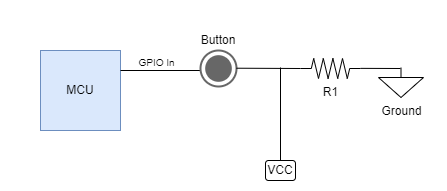
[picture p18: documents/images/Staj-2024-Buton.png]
ButtonDiyagram


Şekilde gördüğümüz R1 direnci VCC'ye göre belirlenmelidir. MCU'nun 3.3v maksimum çalışma gerilimine sahip olduğunu düşünürsek, giriş voltajı kesinlikle 3.3 voltu geçmemelidir. VCC MCU'nun kendisinden alınabileceği gibi, güç kaynağından da alınabilir. Ancak butonlarda yüksek akıma ihtiyaç olmadığı için VCC hattını doğrudan MCU'dan çekmek mantıklı bir seçenektir.

**Önemli Not:** VCC gerilimi MCU'nun kabul edeceği seviyede olsa bile direnç kullanılması zorunludur. Aksi taktirde buton aktif hale getirilse bile akım dirençsiz yoldan geçeceği için MCU tarafından okuma sağlanamayacaktır.

## Debounce Nedir?
Mekanik butonlar, fiziksel olarak iki temas yüzeyinin birbirine dokunması ve sonra ayrılmasıyla çalışır. Butona basıldığında, temas noktaları bir süreliğine geçici olarak açılıp kapanabilir. Bu durum, birkaç mikrosaniyelik titreşimlere neden olur ve "bouncing" olarak bilinir. Bouncing, bir butona basıldığında veya bırakıldığında, temas noktalarının birkaç kez açılıp kapanmasına yol açar. Bu da MCU yazılımının kararsız kalmasına ve hatalı işlem yapmasına sebep olur. Bu durumu gidermek için bazı yöntemler bulunmaktadır. İşte bu yöntemler:

- Yeteri kadar büyük bir direnç kullanmak. Direnç kullanılarak gürültüler önemli ölçüde azaltılabilir. 
- Kapasitör kullanmak. Butonla MCU arasındaki hatta kapasitör ekleyerek dalgalanmaların önüne geçilerek düzgün bir voltaj sağlanabilir.
- Yazılım çözümleri. Firmware yazılımında sinyalin belli bir süre stabil gelmesinden sonra doğru kabul edileceğine yönelik eklemeler yapılarak çözüm bulunabilir.

Yukarıdaki yöntemlerin tümünü aynı anda kullanmak en efektif sonucu verecektir. Yine de proje durumuna göre yalnızca bir tanesi de kullanılabilir. 

Bouncing durumunun ölçüm cihazlarıyla kaydedilmiş görselleri:
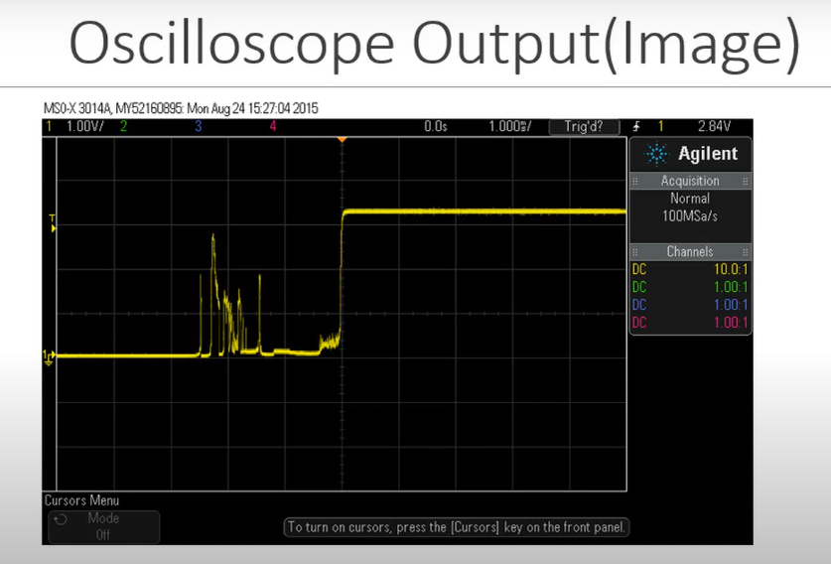
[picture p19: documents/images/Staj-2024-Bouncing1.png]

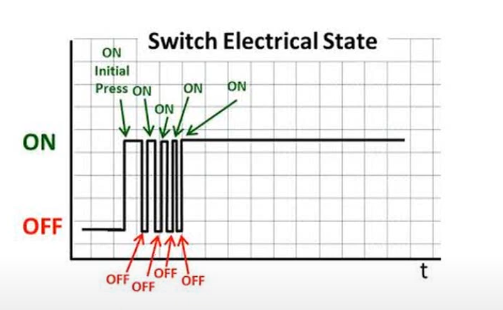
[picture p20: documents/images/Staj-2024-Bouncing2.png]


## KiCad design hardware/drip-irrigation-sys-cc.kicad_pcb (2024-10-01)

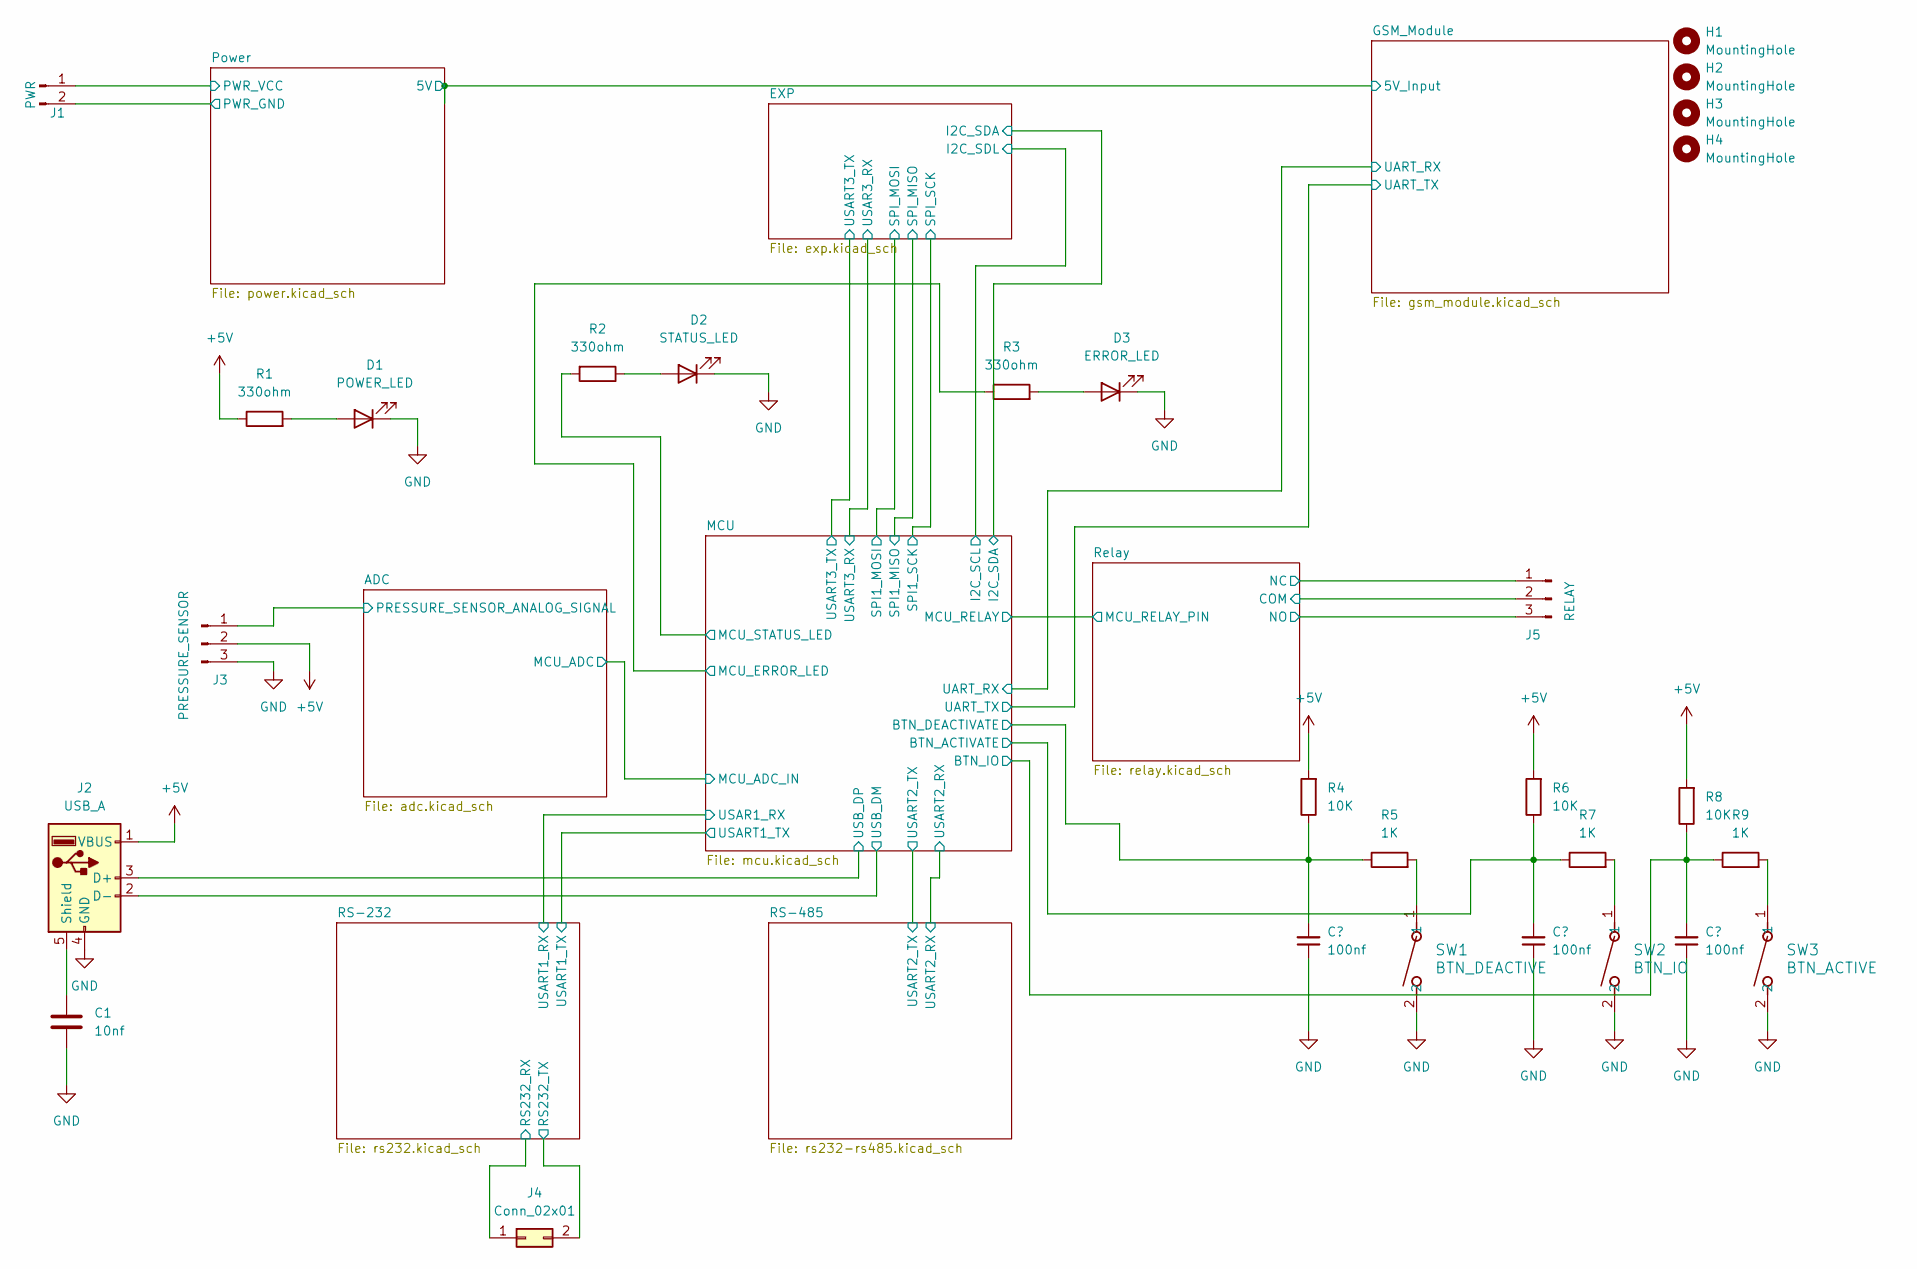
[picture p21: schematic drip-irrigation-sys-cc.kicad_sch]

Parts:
C1: 10nf; C_0805_2012Metric
C2, C3, C4: 100nf; C_0805_2012Metric
D1: POWER_LED; LED_0805_2012Metric
D2: STATUS_LED; LED_0805_2012Metric
D3: ERROR_LED; LED_0805_2012Metric
H1, H2, H3, H4: MountingHole; MountingHole_2.5mm
J1: PWR; PhoenixContact_MSTBA_2,5_2-G-5,08_1x02_P5.08mm_Horizontal
J2: USB_A; CONN4X1_UJ2-AV-4-SMT-TR_CUD
J3: PRESSURE_SENSOR; PhoenixContact_MSTBA_2,5_3-G_1x03_P5.00mm_Horizontal
J4: Conn_02x01; PhoenixContact_MCV_1,5_2-G-3.81_1x02_P3.81mm_Vertical
J5: RELAY; PhoenixContact_MSTBA_2,5_3-G_1x03_P5.00mm_Horizontal
R1, R2, R3: 330ohm; R_0603_1608Metric
R4, R6, R8: 10K; R_0603_1608Metric
R5, R7, R9: 1K; R_0603_1608Metric; Digikey 311-1.00KHRTR-ND
SW1: BTN_DEACTIVE; SW_PTS636_CNK; Digikey CKN12319-2-ND
SW2: BTN_IO; SW_PTS636_CNK; Digikey CKN12319-2-ND
SW3: BTN_ACTIVE; SW_PTS636_CNK; Digikey CKN12319-2-ND

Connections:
+5V: J2.1 (VBUS), J3.2, R1.1, R4.2, R6.2, R8.2; also elsewhere on the board
/ADC/PRESSURE_SENSOR_ANALOG_SIGNAL: J3.1; also elsewhere on the board
/MCU/BTN_ACTIVATE: C3.2, R6.1, R7.1; also elsewhere on the board
/MCU/BTN_DEACTIVATE: C2.2, R4.1, R5.1; also elsewhere on the board
/MCU/BTN_IO: C4.2, R8.1, R9.1; also elsewhere on the board
/MCU/MCU_ERROR_LED: R3.1; also elsewhere on the board
/MCU/MCU_STATUS_LED: R2.2; also elsewhere on the board
/MCU/USB_DM: J2.2 (D-); also elsewhere on the board
/MCU/USB_DP: J2.3 (D+); also elsewhere on the board
/Power/PWR_GND: J1.2; also elsewhere on the board
/Power/PWR_VCC: J1.1; also elsewhere on the board
/RS-232/RS232_RX: J4.1; also elsewhere on the board
/RS-232/RS232_TX: J4.2; also elsewhere on the board
/Relay/COM: J5.2; also elsewhere on the board
/Relay/NC: J5.1; also elsewhere on the board
/Relay/NO: J5.3; also elsewhere on the board
GND: C1.2, C2.1, C3.1, C4.1, D1.1 (K), D2.1 (K), D3.1 (K), J2.4 (GND), J3.3, SW1.2, SW2.2, SW3.2; also elsewhere on the board
unnamed: D1.2 (A), R1.2
unnamed: D2.2 (A), R2.1
unnamed: D3.2 (A), R3.2
unnamed: C1.1, J2.5 (Shield)
unnamed: R7.2, SW2.1
unnamed: R9.2, SW3.1

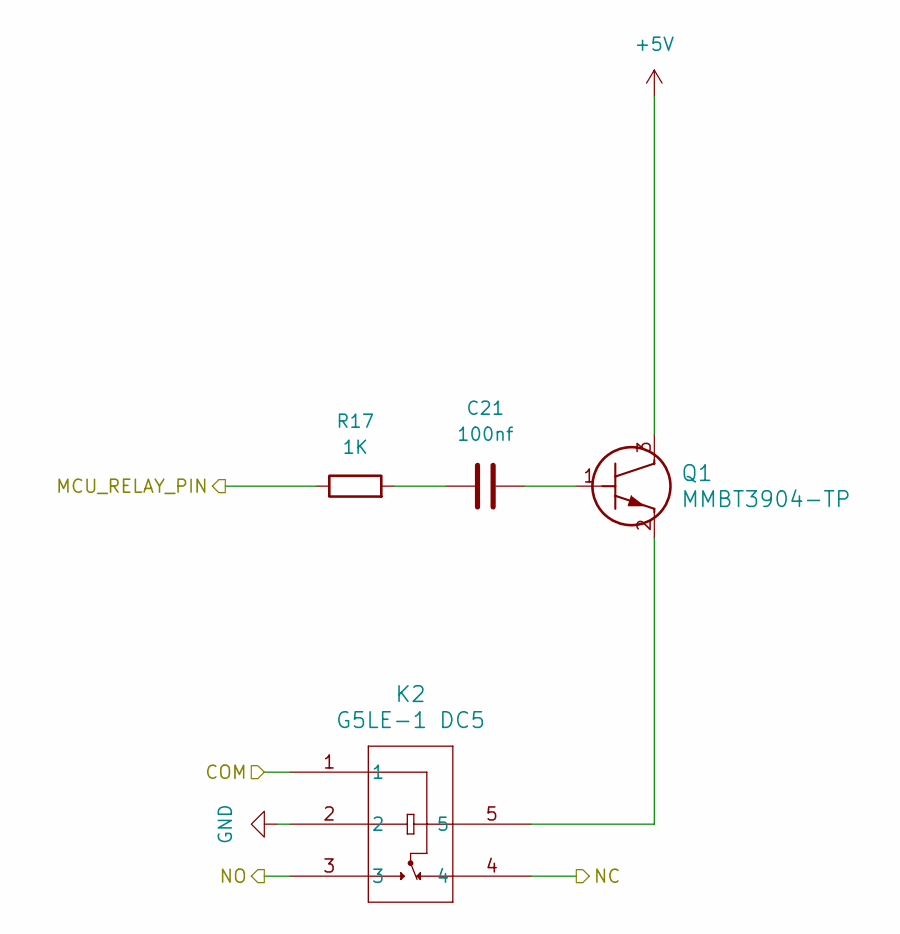
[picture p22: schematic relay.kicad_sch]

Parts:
C21: 100nf; C_0805_2012Metric
K2: G5LE-1 DC5; RELAY_G5LE-1 DC5_OMR
Q1: MMBT3904-TP; SOT-23_MCC; Digikey MMBT3904TPMSTR-ND
R17: 1K; R_0603_1608Metric

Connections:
+5V: Q1.3; also elsewhere on the board
/MCU/MCU_RELAY: R17.1; also elsewhere on the board
/Relay/COM: K2.1; also elsewhere on the board
/Relay/NC: K2.4; also elsewhere on the board
/Relay/NO: K2.3; also elsewhere on the board
GND: K2.2; also elsewhere on the board
unnamed: C21.1, R17.2
unnamed: C21.2, Q1.1
unnamed: K2.5, Q1.2

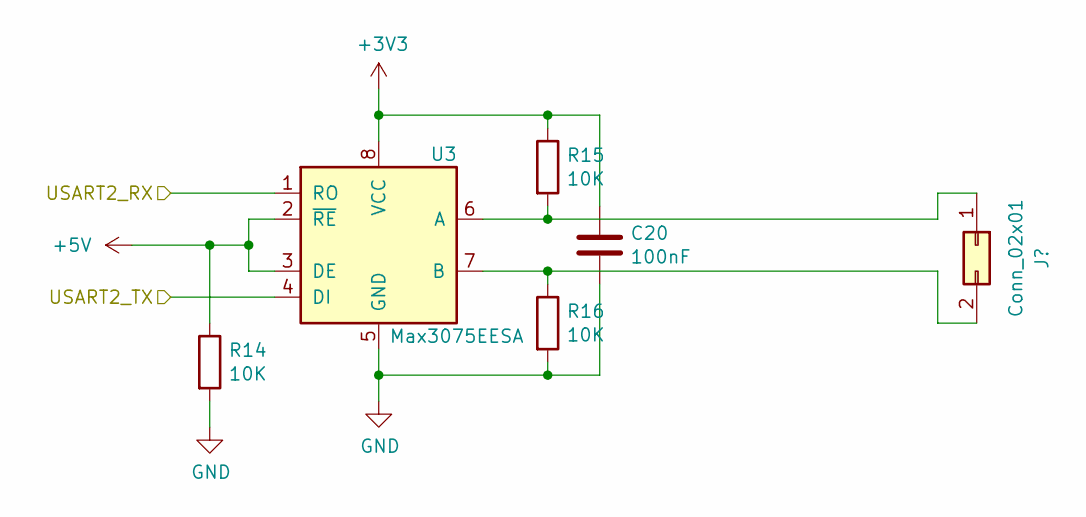
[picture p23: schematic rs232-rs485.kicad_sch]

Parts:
C20: 100nF; C_0805_2012Metric; Digikey 311-1343-6-ND
J8: Conn_02x01; PhoenixContact_MCV_1,5_2-G-3.81_1x02_P3.81mm_Vertical
R14, R15, R16: 10K; R_0603_1608Metric; Digikey 311-10.0KHRDKR-ND
U3: Max3075EESA; SOIC-8_3.9x4.9mm_P1.27mm; DIGIKEY_PART_NUMBER MAX3075EESA+-ND

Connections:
+3V3: C20.1, R15.1, U3.8 (VCC); also elsewhere on the board
+5V: R14.1, U3.2 (~RE), U3.3 (DE); also elsewhere on the board
/MCU/USART2_RX: U3.1 (RO); also elsewhere on the board
/MCU/USART2_TX: U3.4 (DI); also elsewhere on the board
GND: C20.2, R14.2, R16.2, U3.5 (GND); also elsewhere on the board
unnamed: J8.1, R15.2, U3.6 (A)
unnamed: J8.2, R16.1, U3.7 (B)

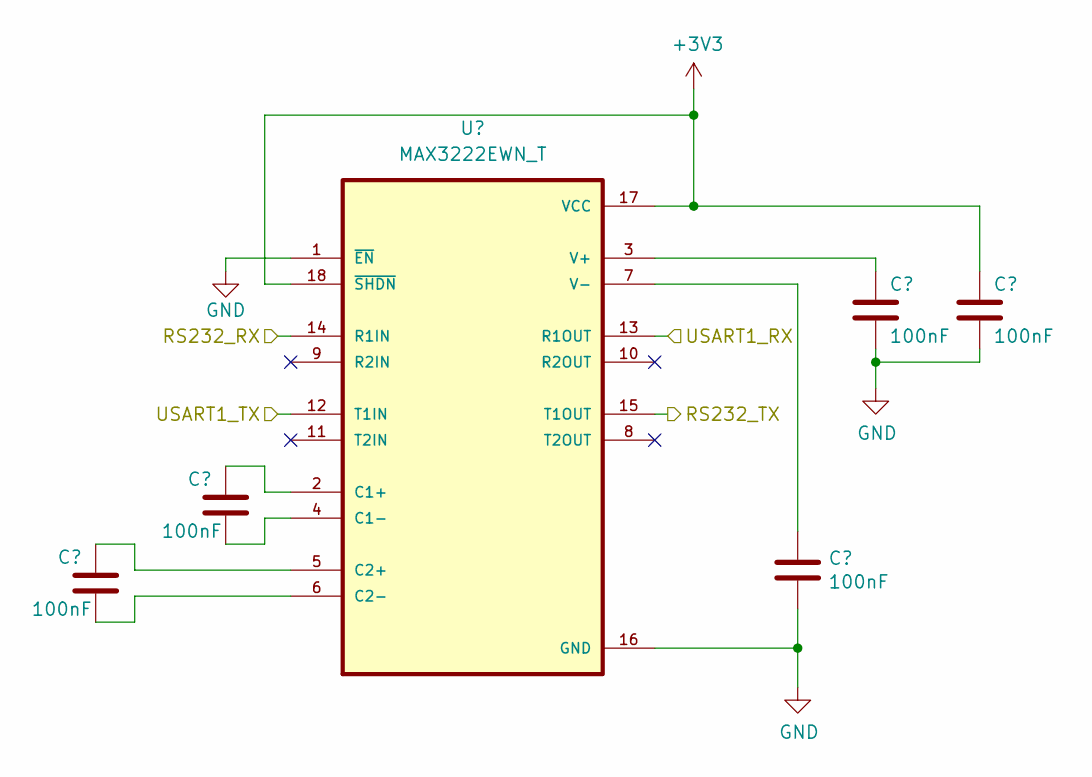
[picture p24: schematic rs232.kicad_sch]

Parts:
C15, C16, C17, C18, C19: 100nF; C_0805_2012Metric; Digikey 311-1343-6-ND
U2: MAX3222EWN_T; MAX3222EWN+T; Digikey MAX3222EWN+TTR-ND

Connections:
+3V3: C19.1, U2.17 (VCC), U2.18 (~SHDN); also elsewhere on the board
/MCU/USAR1_RX: U2.13 (R1OUT); also elsewhere on the board
/MCU/USART1_TX: U2.12 (T1IN); also elsewhere on the board
/RS-232/RS232_RX: U2.14 (R1IN); also elsewhere on the board
/RS-232/RS232_TX: U2.15 (T1OUT); also elsewhere on the board
GND: C17.2, C18.2, C19.2, U2.1 (~EN), U2.16 (GND); also elsewhere on the board
unnamed: C16.1, U2.2 (C1+)
unnamed: C16.2, U2.4 (C1-)
unnamed: C15.1, U2.5 (C2+)
unnamed: C15.2, U2.6 (C2-)
unnamed: C18.1, U2.3 (V+)
unnamed: C17.1, U2.7 (V-)

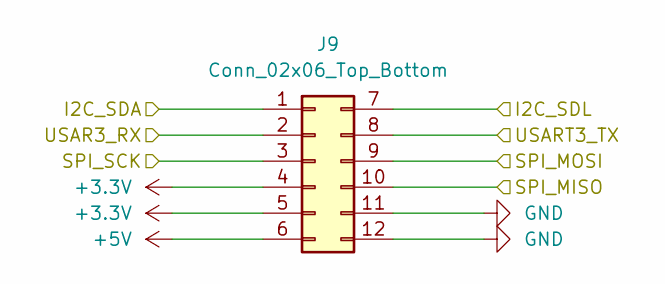
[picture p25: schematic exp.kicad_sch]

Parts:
J9: Conn_02x06_Top_Bottom; PinHeader_2x06_P2.54mm_Vertical

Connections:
+3.3V: J9.4, J9.5; also elsewhere on the board
+5V: J9.6; also elsewhere on the board
/EXP/I2C_SDA: J9.1; also elsewhere on the board
/EXP/I2C_SDL: J9.7; also elsewhere on the board
/EXP/SPI_MISO: J9.10; also elsewhere on the board
/EXP/SPI_MOSI: J9.9; also elsewhere on the board
/EXP/SPI_SCK: J9.3; also elsewhere on the board
/EXP/USAR3_RX: J9.2; also elsewhere on the board
/EXP/USART3_TX: J9.8; also elsewhere on the board
GND: J9.11, J9.12; also elsewhere on the board

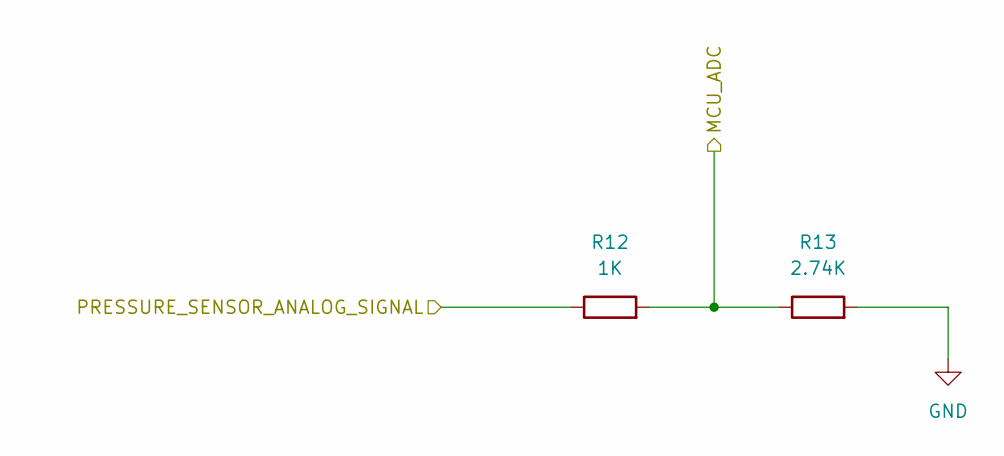
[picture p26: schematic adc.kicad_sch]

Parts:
R12: 1K; R_0603_1608Metric; Digikey 311-1.00KHRDKR-ND
R13: 2.74K; R_0603_1608Metric; Digikey 311-2.74KHRDKR-ND

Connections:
/ADC/MCU_ADC: R12.2, R13.1; also elsewhere on the board
/ADC/PRESSURE_SENSOR_ANALOG_SIGNAL: R12.1; also elsewhere on the board
GND: R13.2; also elsewhere on the board

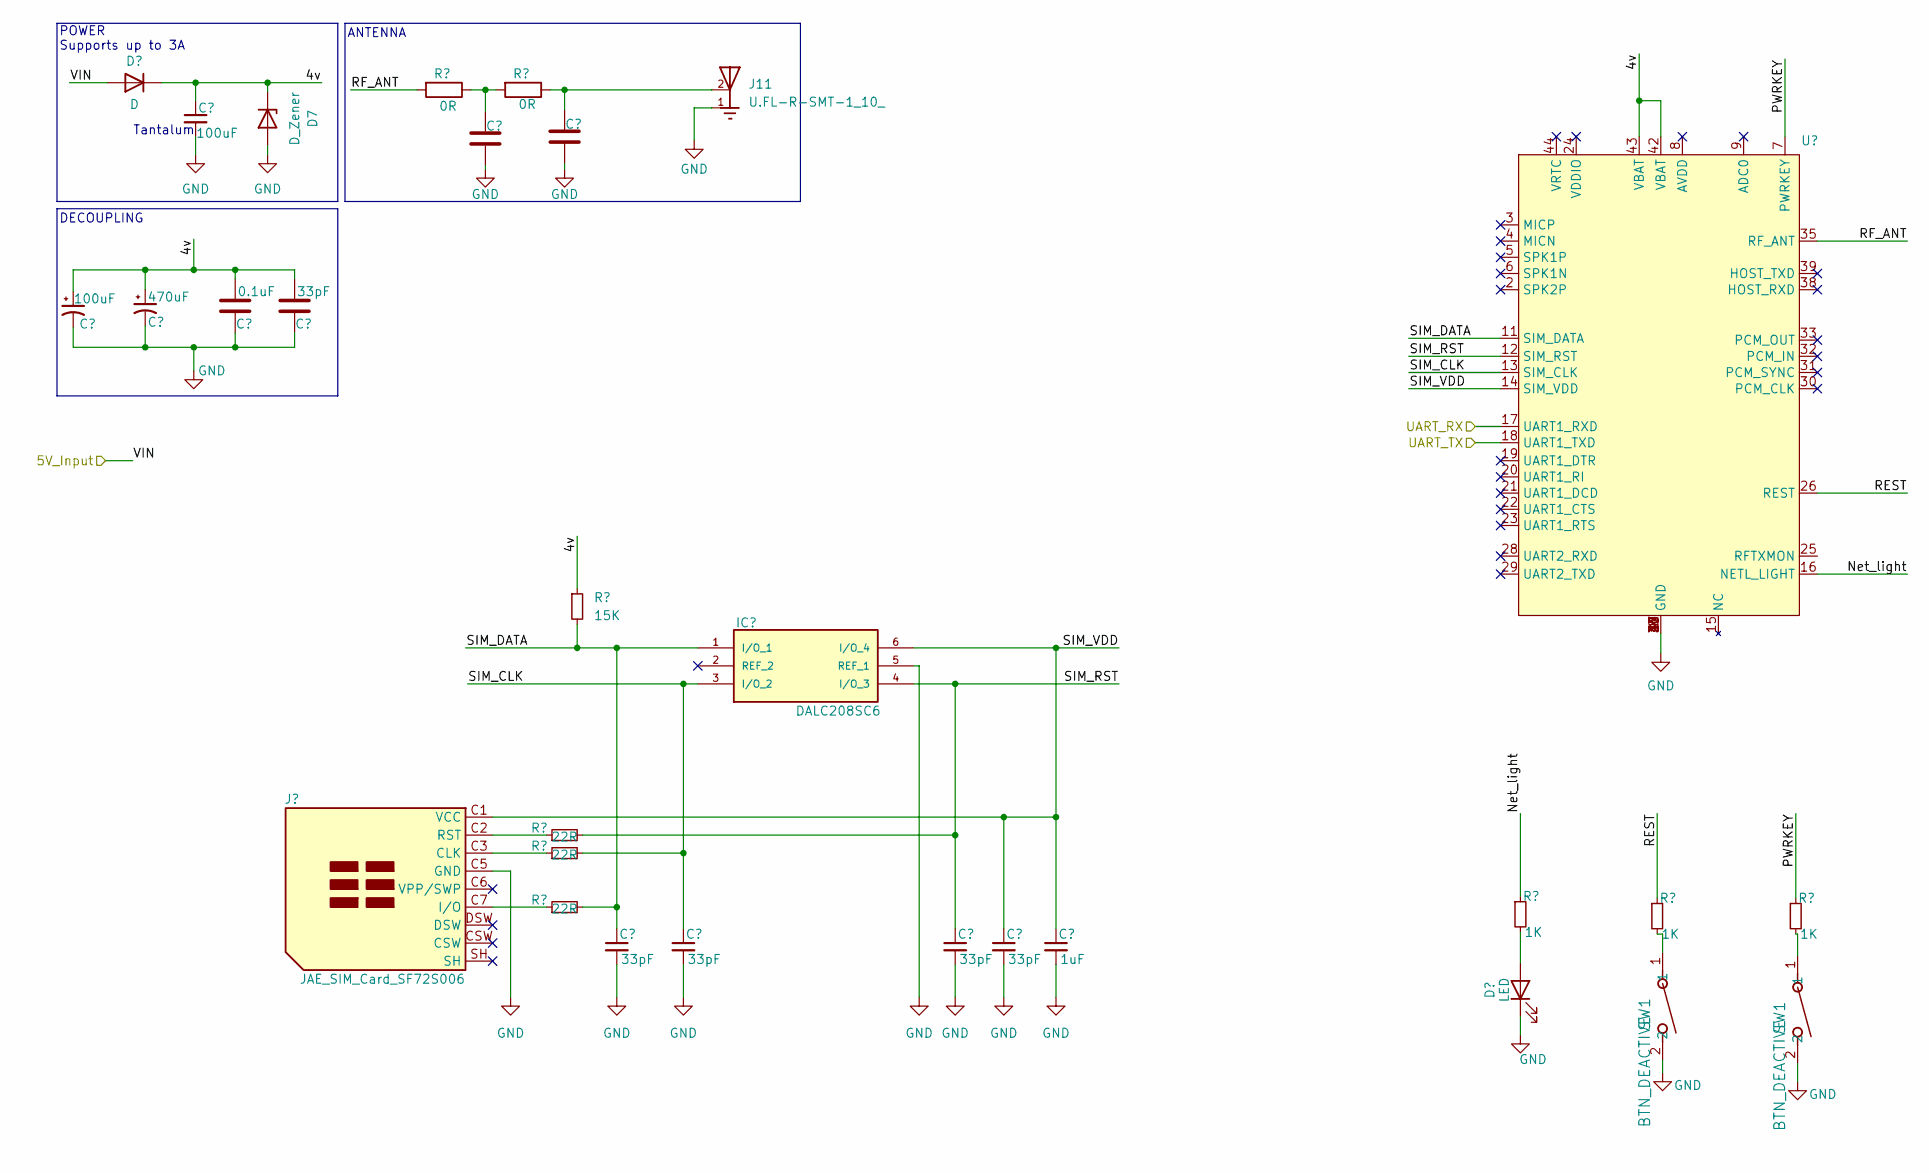
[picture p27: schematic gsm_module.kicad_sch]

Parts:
C28: 100uF; CP_Elec_8x10.5
C29: 470uF; CP_Elec_8x10.5
C30: 100uF; CP_EIA-6032-15_Kemet-U; Digikey TCKOJ107CT
C31: 0.1uF; C_0805_2012Metric
C32, C35, C36, C37, C38: 33pF; C_0805_2012Metric
C33, C34: C_0805_2012Metric
C39: 1uF; C_0805_2012Metric
D6: D; D_SOD-123F; Digikey NRVHP220SFT3GOSTR-ND
D7: D_Zener; SMB-2_4P60X3P95_ONS; Digikey SZ1SMB5915BT3GOSTR-ND
D8: LED; LED_0805_2012Metric
IC1: DALC208SC6; SOT23-6L_STM; Digikey 497-2525-2-ND
J10: JAE_SIM_Card_SF72S006
J11: U.FL-R-SMT-1_10_; HRS_U.FL-R-SMT-1_10_
R18, R19: 0R; R_0603_1608Metric
R20, R21, R22: 22R; R_0603_1608Metric
R23: 15K; R_0603_1608Metric
R24, R25, R26: 1K; R_0603_1608Metric
SW1: BTN_DEACTIVE; SW_PTS636_CNK; Digikey CKN12319-2-ND
U6: MG2608

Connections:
+5V: D6.2 (A); also elsewhere on the board
/GSM_Module/4v: C28.1, C29.1, C30.1, C31.1, C32.1, D6.1 (K), D7.1 (K), R23.1, U6.42 (VBAT), U6.43 (VBAT)
/GSM_Module/Net_light: R24.1, U6.16 (NETL_LIGHT)
/GSM_Module/PWRKEY: R26.1, U6.7 (PWRKEY)
/GSM_Module/REST: R25.1, U6.26 (REST)
/GSM_Module/RF_ANT: R18.2, U6.35 (RF_ANT)
/GSM_Module/SIM_CLK: C36.1, IC1.3 (I/O_2), R21.2, U6.13 (SIM_CLK)
/GSM_Module/SIM_DATA: C35.1, IC1.1 (I/O_1), R22.2, R23.2, U6.11 (SIM_DATA)
/GSM_Module/SIM_RST: C37.1, IC1.4 (I/O_3), R20.2, U6.12 (SIM_RST)
/GSM_Module/SIM_VDD: C38.1, C39.1, IC1.6 (I/O_4), J10.C1 (VCC), U6.14 (SIM_VDD)
/GSM_Module/UART_RX: U6.17 (UART1_RXD); also elsewhere on the board
/GSM_Module/UART_TX: U6.18 (UART1_TXD); also elsewhere on the board
GND: C28.2, C29.2, C30.2, C31.2, C32.2, C33.2, C34.2, C35.2, C36.2, C37.2, C38.2, C39.2, D7.2 (A), D8.1 (K), IC1.5 (REF_1), J10.C5 (GND), J11.1, SW1.2, U6.1 (GND), U6.10 (GND), U6.27 (GND), U6.34 (GND), U6.36 (GND), U6.37 (GND), U6.40 (GND), U6.41 (GND); also elsewhere on the board
unnamed: C33.1, R18.1, R19.2
unnamed: C34.1, J11.2, R19.1
unnamed: D8.2 (A), R24.2
unnamed: J10.C3 (CLK), R21.1
unnamed: J10.C7 (I/O), R22.1
unnamed: J10.C2 (RST), R20.1

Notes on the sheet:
DECOUPLING
ANTENNA
POWER Supports up to 3A
Tantalum

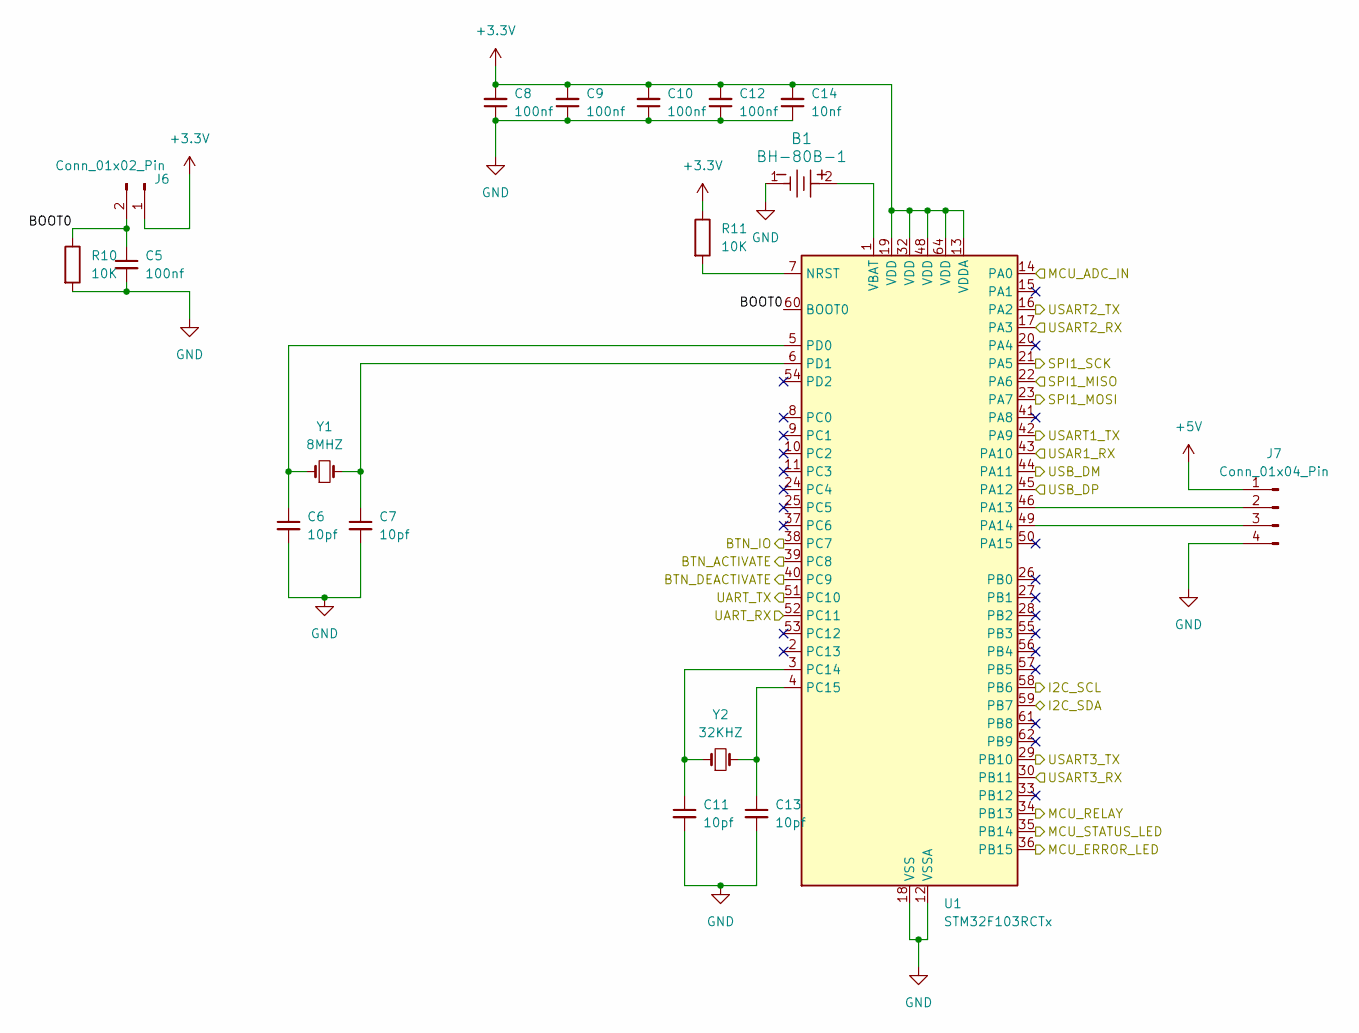
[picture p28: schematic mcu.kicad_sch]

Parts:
B1: BH-80B-1; BH-80B-1_ADM; Digikey 2057-BH-80B-1-ND
C5, C8, C9, C10, C12: 100nf; C_0805_2012Metric
C6, C7, C11, C13: 10pf; C_0805_2012Metric
C14: 10nf; C_0805_2012Metric
J6: Conn_01x02_Pin; PinHeader_1x02_P2.54mm_Vertical
J7: Conn_01x04_Pin; PinHeader_1x04_P2.54mm_Vertical
R10, R11: 10K; R_0603_1608Metric
U1: STM32F103RCTx; LQFP-64_10x10mm_P0.5mm
Y1: 8MHZ; XTAL_ABLS2_ABR; Digikey 535-10212-2-ND
Y2: 32KHZ; XTAL_CM7V-T1A_MCX; Digikey 2195-CM7V-T1A-32.768KHZ-7PF-20PPM-TB-QA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

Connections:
+3.3V: C8.2, C9.2, C10.2, C12.2, C14.2, J6.1, R11.1, U1.13 (VDDA), U1.19 (VDD), U1.32 (VDD), U1.48 (VDD), U1.64 (VDD); also elsewhere on the board
+5V: J7.1; also elsewhere on the board
/ADC/MCU_ADC: U1.14 (PA0); also elsewhere on the board
/EXP/I2C_SDA: U1.59 (PB7); also elsewhere on the board
/EXP/I2C_SDL: U1.58 (PB6); also elsewhere on the board
/EXP/SPI_MISO: U1.22 (PA6); also elsewhere on the board
/EXP/SPI_MOSI: U1.23 (PA7); also elsewhere on the board
/EXP/SPI_SCK: U1.21 (PA5); also elsewhere on the board
/EXP/USAR3_RX: U1.30 (PB11); also elsewhere on the board
/EXP/USART3_TX: U1.29 (PB10); also elsewhere on the board
/GSM_Module/UART_RX: U1.52 (PC11); also elsewhere on the board
/GSM_Module/UART_TX: U1.51 (PC10); also elsewhere on the board
/MCU/BOOT0: C5.1, J6.2, R10.1, U1.60 (BOOT0)
/MCU/BTN_ACTIVATE: U1.39 (PC8); also elsewhere on the board
/MCU/BTN_DEACTIVATE: U1.40 (PC9); also elsewhere on the board
/MCU/BTN_IO: U1.38 (PC7); also elsewhere on the board
/MCU/MCU_ERROR_LED: U1.36 (PB15); also elsewhere on the board
/MCU/MCU_RELAY: U1.34 (PB13); also elsewhere on the board
/MCU/MCU_STATUS_LED: U1.35 (PB14); also elsewhere on the board
/MCU/USAR1_RX: U1.43 (PA10); also elsewhere on the board
/MCU/USART1_TX: U1.42 (PA9); also elsewhere on the board
/MCU/USART2_RX: U1.17 (PA3); also elsewhere on the board
/MCU/USART2_TX: U1.16 (PA2); also elsewhere on the board
/MCU/USB_DM: U1.44 (PA11); also elsewhere on the board
/MCU/USB_DP: U1.45 (PA12); also elsewhere on the board
GND: B1.1, C5.2, C6.2, C7.2, C8.1, C9.1, C10.1, C11.2, C12.1, C13.2, C14.1, J7.4, R10.2, U1.12 (VSSA), U1.18 (VSS), U1.31 (VSS), U1.47 (VSS), U1.63 (VSS); also elsewhere on the board
unnamed: J7.2, U1.46 (PA13)
unnamed: J7.3, U1.49 (PA14)
unnamed: R11.2, U1.7 (NRST)
unnamed: C11.1, U1.3 (PC14), Y2.1
unnamed: C13.1, U1.4 (PC15), Y2.2
unnamed: C6.1, U1.5 (PD0), Y1.1
unnamed: C7.1, U1.6 (PD1), Y1.2
unnamed: B1.2, U1.1 (VBAT)

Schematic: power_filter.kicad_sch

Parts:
C22, C23: 33nf; C_0805_2012Metric
D4: D; DIODE_DO214AA_MBRS_VIS; Digikey SSB44-E3/52TGIDKR-ND
F1: Fuse; Fuse_0603_1608Metric; Digikey 507-1098-6-ND
L1: PA2743NL; POLECAT_PA2743NL_PUL; Digikey 553-2181-ND

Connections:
+12V: C23.1, L1.3; also elsewhere on the board
/Power/PWR_GND: C22.2, L1.2; also elsewhere on the board
/Power/PWR_VCC: F1.1; also elsewhere on the board
GND: C23.2, L1.4; also elsewhere on the board
unnamed: D4.2 (A), F1.2
unnamed: C22.1, D4.1 (K), L1.1

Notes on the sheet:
Filter

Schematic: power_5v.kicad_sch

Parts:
C26: 100uf; CAP_WCAP-ASLI_06p3X05p5_WRE; Digikey 732-8419-2-ND
C27: 330uf; PCAP_8x10-ELECT_NCA; Digikey 493-2193-2-ND
D5: 1N5822; DO-201AD_STM; Digikey 497-11370-1-ND
L2: 330uh; L_12x12mm_H8mm; Digikey 553-3620-6-ND
U5: LM2576-5.0WU-TR; Digikey LM2576-5.0WU-TR-ND

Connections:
+5V: C27.1, L2.2, U5.4 (FEEDBACK); also elsewhere on the board
+12V: C26.1, U5.1 (VIN); also elsewhere on the board
GND: C26.2, C27.2, D5.2 (A), U5.3 (GROUND), U5.5 (*ON/OFF); also elsewhere on the board
unnamed: D5.1 (K), L2.1, U5.2 (OUTPUT)

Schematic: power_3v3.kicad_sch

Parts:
C24, C25: 1uf; C_0201_0603Metric; Digikey 490-7229-2-ND
U4: MIC5504-3.3YM5-TR; Digikey MIC5504-3.3YM5-TR

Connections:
+3.3V: C25.1, U4.5 (VOUT); also elsewhere on the board
+5V: C24.1, U4.1 (VIN), U4.3 (EN); also elsewhere on the board
GND: C24.2, C25.2, U4.2 (GND); also elsewhere on the board

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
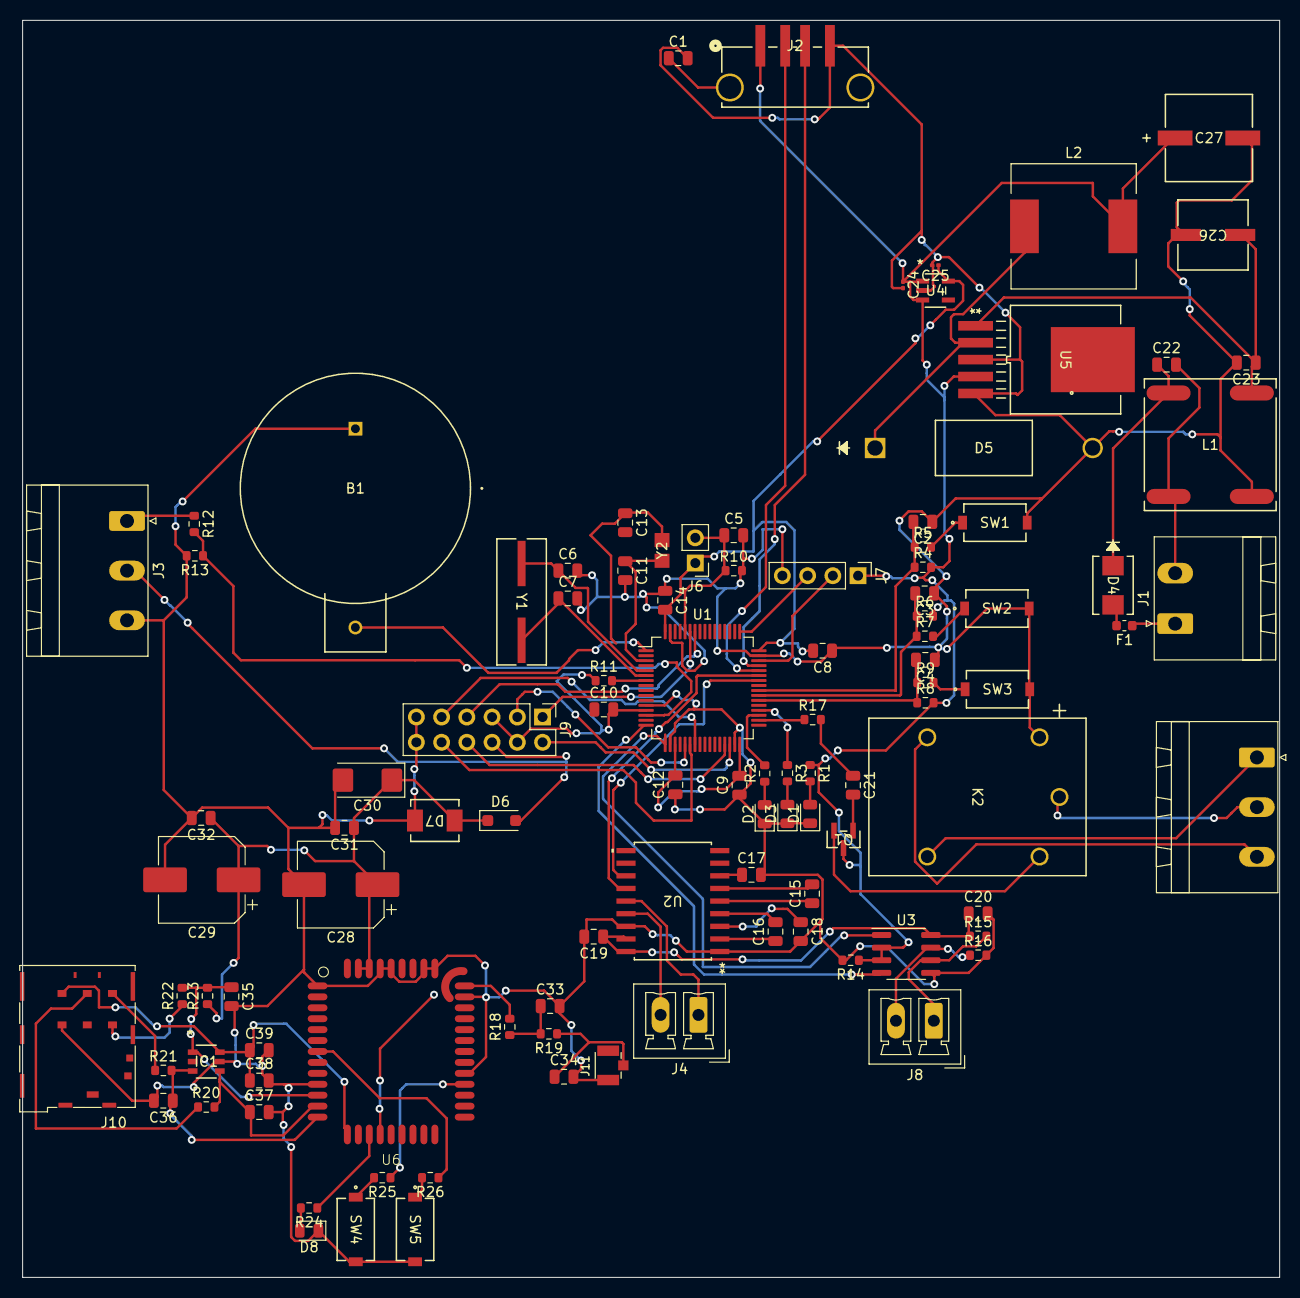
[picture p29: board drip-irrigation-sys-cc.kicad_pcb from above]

Board: 2 copper layers, 126.5 x 126.5 mm, 108 parts (0 on the bottom side), 82 nets.

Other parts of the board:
SW4, SW5: BTN_DEACTIVE; SW_PTS636_CNK

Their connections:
GND: SW4.2, SW5.2; also elsewhere on the board

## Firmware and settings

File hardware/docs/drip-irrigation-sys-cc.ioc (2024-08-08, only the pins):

Mcu.UserName=STM32F103RCTx
PA0-WKUP.Signal=ADCx_IN0
PA10.Signal=USART1_RX
PA11.Signal=USB_DM
PA12.Signal=USB_DP
PA13.Signal=SYS_JTMS-SWDIO
PA14.Signal=SYS_JTCK-SWCLK
PA2.Signal=USART2_TX
PA3.Signal=USART2_RX
PA5.Signal=SPI1_SCK
PA6.Signal=SPI1_MISO
PA7.Signal=SPI1_MOSI
PA9.Signal=USART1_TX
PB10.Signal=USART3_TX
PB11.Signal=USART3_RX
PB13.GPIO_Label=RELAY
PB13.Signal=GPIO_Output
PB14.GPIO_Label=LED_STATUS
PB14.Signal=GPIO_Output
PB15.GPIO_Label=LED_ERROR
PB15.Signal=GPIO_Output
PB6.Signal=I2C1_SCL
PB7.Signal=I2C1_SDA
PC10.Signal=UART4_TX
PC11.Signal=UART4_RX
PC14-OSC32_IN.Signal=RCC_OSC32_IN
PC15-OSC32_OUT.Signal=RCC_OSC32_OUT
PC7.GPIO_Label=BTN_IO
PC7.Signal=GPXTI7
PC8.GPIO_Label=BTN_ACTIVE
PC8.Signal=GPXTI8
PC9.GPIO_Label=BTN_DEACTIVE
PC9.Signal=GPXTI9
PD0-OSC_IN.Signal=RCC_OSC_IN
PD1-OSC_OUT.Signal=RCC_OSC_OUT

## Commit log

2024-08-08 KiCad projesi olusturuldu.
    [adc.kicad_sch, drip-irrigation-sys-cc.kicad_pcb, drip-irrigation-sys-cc.kicad_sch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]
2024-08-12 Yeni resimler ve diyagramlar eklendi. relay_leds_usage.md dosyası oluşturuldu.
2024-08-12 relay_leds_usage.md dosyası relay_leds_buttons_usage.md olarak düzenlendi. İçeriğinde değişiklikler yapıldı.
2024-08-15 power.md düzenlendi. Yeni görseller eklendi.
2024-08-18 power.kicad_sch düzenlemesi yapıldı.
    [drip-irrigation-sys-cc.kicad_sch, power.kicad_sch, power_12v.kicad_sch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]
2024-08-22 Kicad şema düzenlemesi yapıldı.
    [power.kicad_sch, power_12v.kicad_sch, power_3v3.kicad_sch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]
2024-08-27 Kicad Power Modülü Tamamlandı.
    [mcu.kicad_sch, power.kicad_sch, power_3v3.kicad_sch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]
2024-09-03 Kicad düzenleme.
    [drip-irrigation-sys-cc.kicad_sch, mcu.kicad_sch, mg_2608.kicad_sch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]
2024-09-12 Kicad şema düzenlemesi.
    [gsm_module.kicad_sch, power_5v.kicad_sch]
2024-09-12 Kicad PCB düzenlemesi yapıldı.
    [drip-irrigation-sys-cc.kicad_pcb]
2024-09-18 PCB düzenlemesi yapıldı.
    [drip-irrigation-sys-cc.kicad_pcb, gsm_module.kicad_sch, power_3v3.kicad_sch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]
2024-10-01 PCB düzenlemesi.
    [drip-irrigation-sys-cc.kicad_pcb, gsm_module.kicad_sch, power_filter.kicad_sch]
2024-10-01 PCB düzenleme.
    [drip-irrigation-sys-cc.kicad_sch, gsm_module.kicad_sch, mcu.kicad_sch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]
